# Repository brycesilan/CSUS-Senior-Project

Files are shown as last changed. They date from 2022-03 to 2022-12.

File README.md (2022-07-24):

# CSUS Senior Project
6AC1C5B5-E4C5-4D6C-B1AB-3A2F40A8B9AA

Vertical farming applies modern technologies to revolutionize the traditional agriculture process that has remained unchanged for millennia. Because traditional farming is limited in a 2D space it is very efficient at utilizing a given amount of land for food production. Transitioning the possible area, we can cultivate to a 3D space that can sustain exponentially larger yields than a traditional farm. Vertical farming uses a soilless method of growing food, meaning we can grow the food anywhere in the world with higher yields and fewer resources. With the human population on Earth exploding, the only way we can support the food demands of the future is to expand our food production capabilities into a whole new dimension… Up



A Collaboration with Silicon Valley Mechatronics
Banner2

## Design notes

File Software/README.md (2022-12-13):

# Software for semester 2

Our approach behind this project was to provide users with the hardware (everything connected)
- custom designed control board with loaded components
- Raspberry Pi 4 (With [Client-RaspberryPi](https://github.com/brycesilan/CSUS-Senior-Project/tree/main/Software/Client-RaspberryPi) code on it)
- Arduino Nano (with the [Moisture_pH.ino](https://github.com/brycesilan/CSUS-Senior-Project/blob/main/Software/Arduino/Moisture_pH/Moisture_pH.ino) script loaded on it)
- All the controls (4 pumps, 2 lights, 1 heater and 1 fan) hooked to the control board.
- All sensors (4 soil moisture and 1 pH sensors connected to the Arduino Nano, 1 DHT11 sensor connected to Raspberry Pi)

After setting up their farm, the user would sign up on our web app that was hosted on Firebase and receive a unique userID.

They would replace "User_ID" in [firebase-config.js](https://github.com/brycesilan/CSUS-Senior-Project/blob/main/Software/Client-RaspberryPi/firebase-config.js) and run "node index.js" from the terminal.
This would start sending sensor data to Cloud Firestore and update any controls (from user interface) every 15 seconds.

The user interface provides them with:
- Live sensor readings
- Buttons to control water pumps, lights, heater, and fan.
- Graph of daily readings (from 00:00 to 23:59 for the day)
- Ability to change farm settings (Either use buttons or automate the controls)

The overall goal was to provide the users with hardware and have them setup the farm. 
Then they could sign up on our web app (hosted on Firebase) and interact with their farm from anywhere.

## User Interface
User Interface was developed using Firebase, Cloud Firestore, React, Tailwind CSS, Chart.js.

The webapp developed using Firebase allows you to have multiple users

## Raspberry Pi
Raspberry Pi code developed using Node.js, Firebase, Cloud Firestore.

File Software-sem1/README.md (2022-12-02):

# Software for semester 1 (Archived)
Developed using Python, Flask, Arduino, HTML, Bootstrap

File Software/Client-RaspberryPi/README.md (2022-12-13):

# Client-Raspberry Pi code

The code in this folder runs on the Raspberry Pi.

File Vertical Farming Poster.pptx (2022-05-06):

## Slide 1

Vertical Farming
Elizabeth Tang, Ph.D. Department of Computer Science
College of Engineering and Computer Science

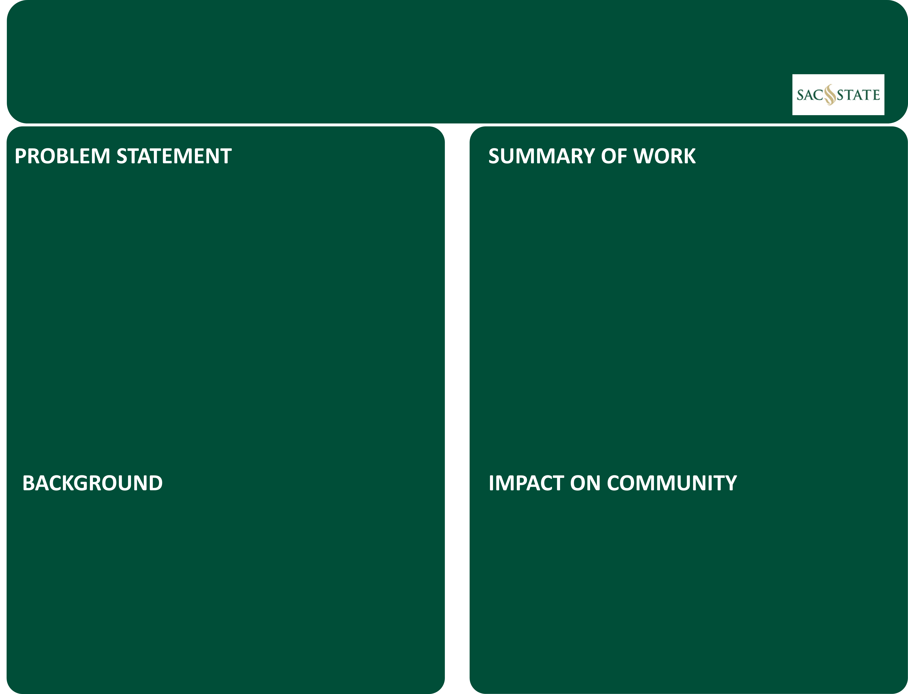
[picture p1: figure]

In this section, explain what you did , what you are doing, or what you plan to do. Keep things relatively simple. Drawings or pictures are often better than equations. Figures may be included here. Be sure to make reference to the Figure(s). In this section, explain what you did , what you are doing, or what you plan to do. Keep things relatively simple. Drawings or pictures are often better than equations. Figures may be included here. Be sure to make reference to the Figure(s).

In one, concise sentence, state what the problem is in laymen’s terms. Make reference to Figure 1 in that sentence.

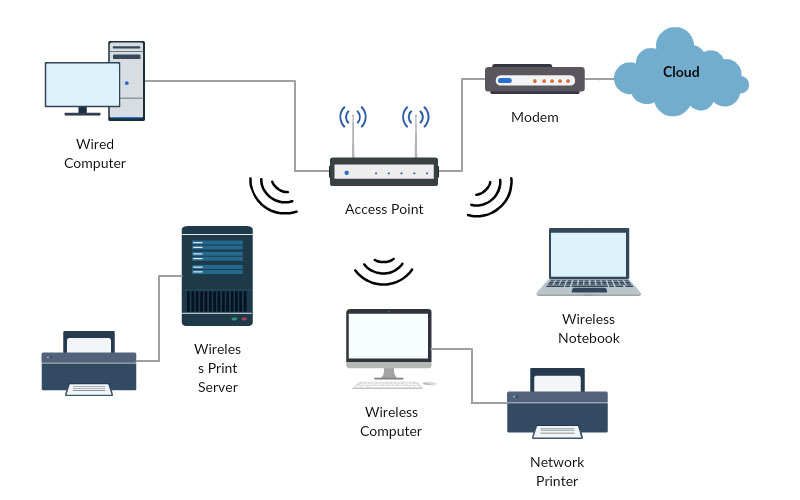
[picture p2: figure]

Figure 1: Add caption here. Add caption here. Add caption here. Add caption here. Add caption here. Add caption here..

In a short paragraph, provide background information necessary to help the guest understand the solution. Figures may be included here. Be sure to make reference to the Figure(s). In a short paragraph, provide background information necessary to help the guest understand the solution. Figures may be included here. Be sure to make reference to the Figure(s). In a short paragraph, provide background information necessary to help the guest understand the solution. Figures may be included here. Be sure to make reference to the Figure(s). In a short paragraph, provide background information necessary to help the guest understand the solution. Figures may be included here. Be sure to make reference to the Figure(s).

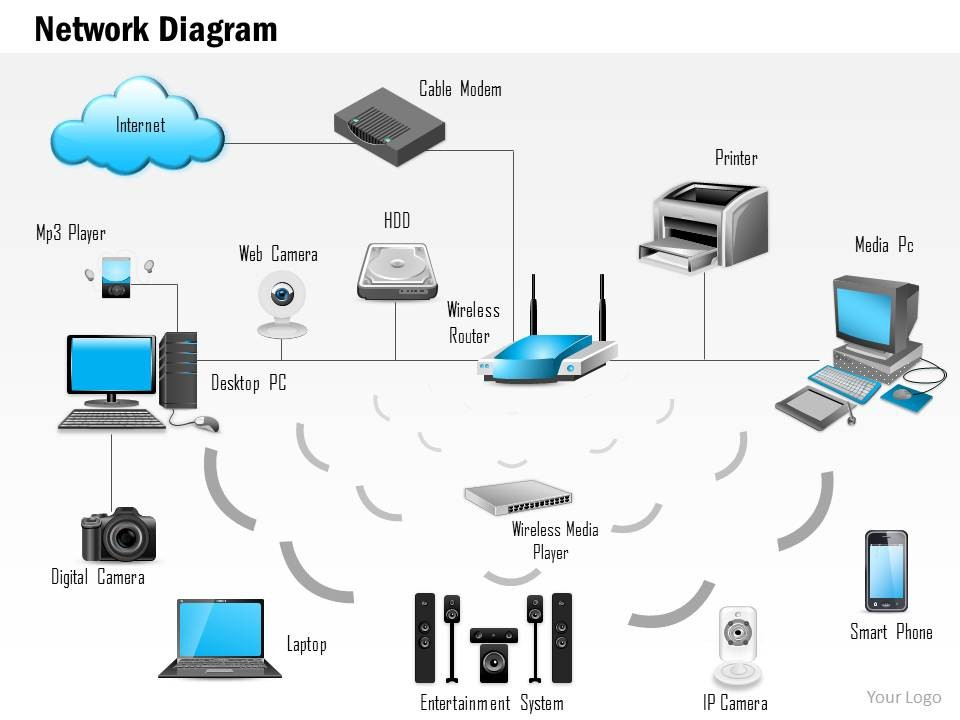
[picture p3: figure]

Figure 2: Add caption here. Add caption here.

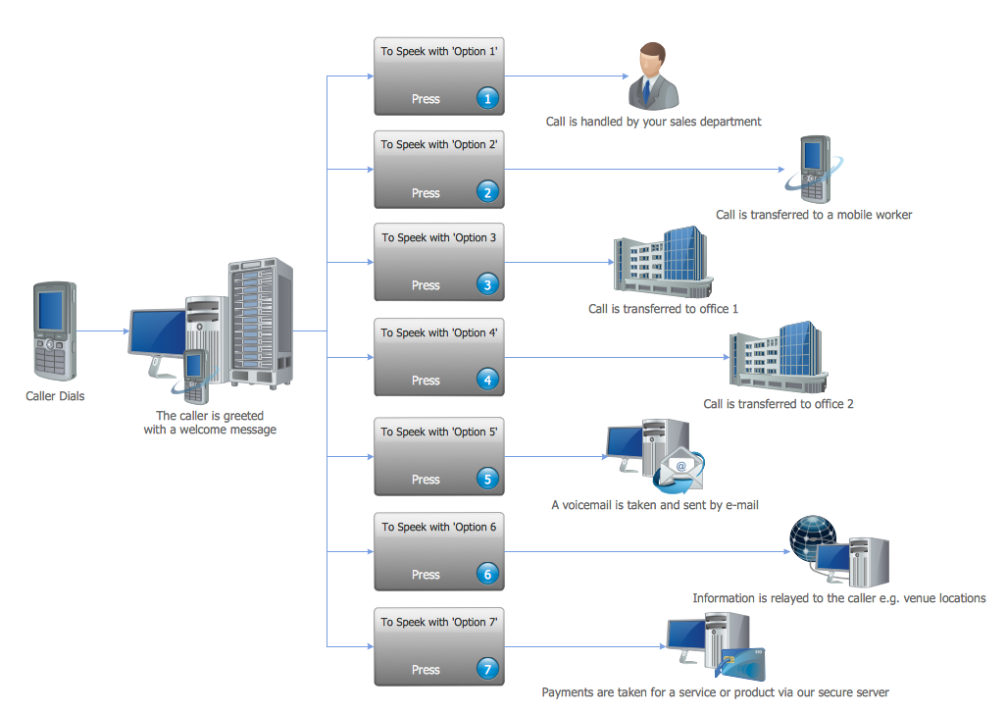
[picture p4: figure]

Figure 3: Add caption here. Add caption here.

What does this mean to the average American or to local industry? What does this mean to the average American or to local industry? What does this mean to the average American or to local industry? What does this mean to the average American or to local industry? What does this mean to the average American or to local industry? Bullet points are suggested:
- Bullet Point 1. Bullet Point 1. Bullet Point 1 . Bullet Point 1
- Bullet Point 2 . Bullet Point 2. Bullet Point 2. Bullet Point 2
- Bullet Point 3 . Bullet Point 2. Bullet Point 3. Bullet Point 3
- Bullet Point 4 . Bullet Point 4. Bullet Point 4..Bullet Point 4

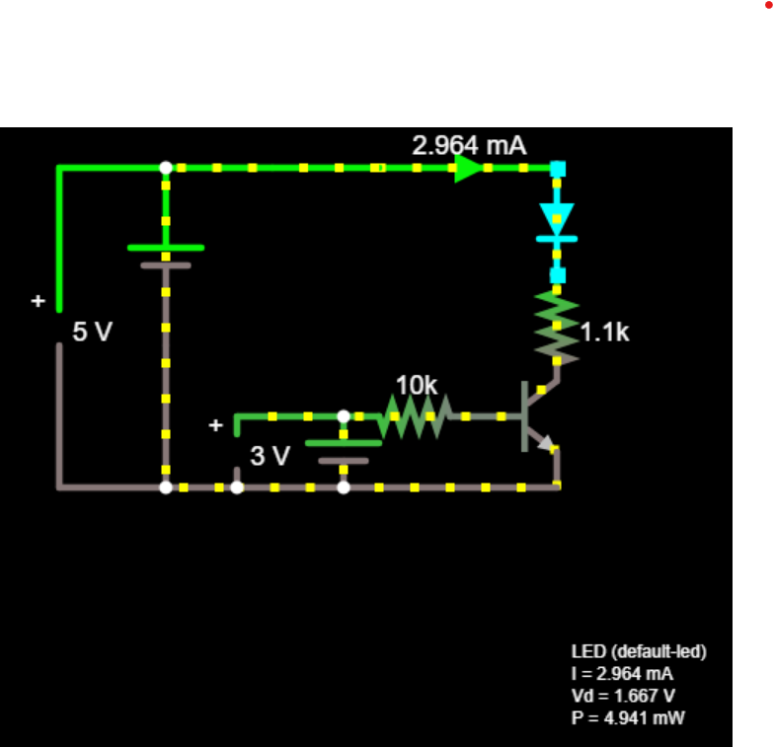
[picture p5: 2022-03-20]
Hardware/Moisture Sensor/Moisture Sensor Rev2/LED_Simulation.png

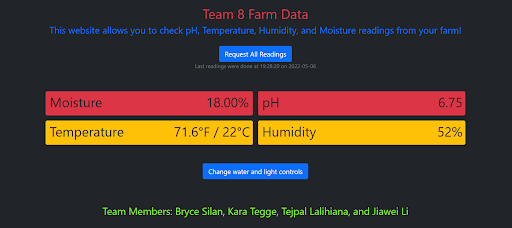
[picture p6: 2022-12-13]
Software-sem1/Screenshots/Readings page-sem 1.png

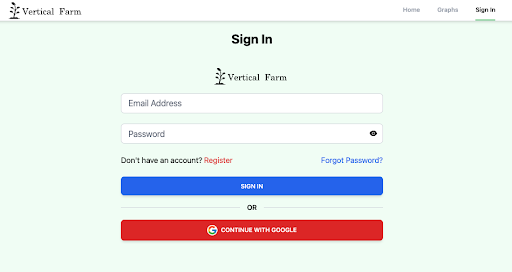
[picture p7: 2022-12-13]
Software/User-Interface/Screenshots/Sign-in page.png

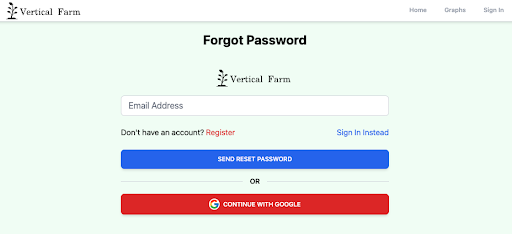
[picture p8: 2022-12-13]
Software/User-Interface/Screenshots/Forgot password page.png

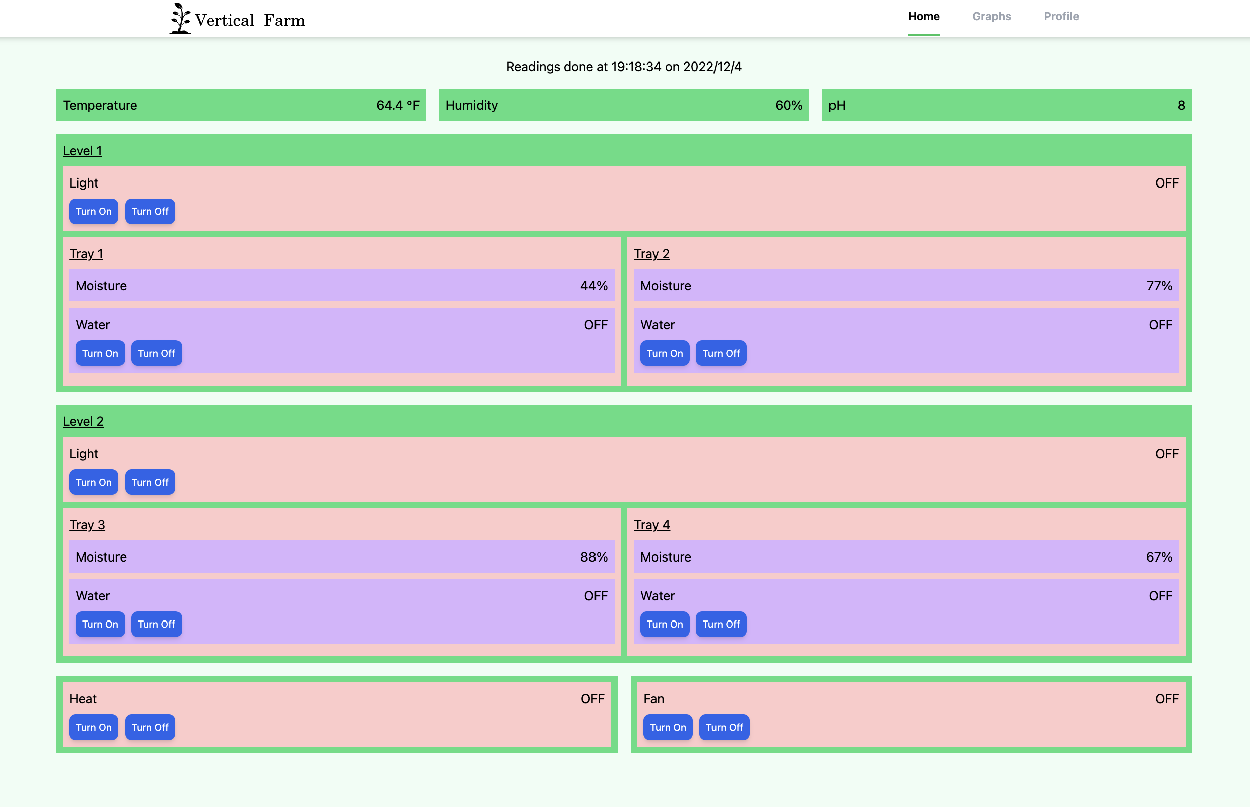
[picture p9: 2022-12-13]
Software/User-Interface/Screenshots/Home page.png

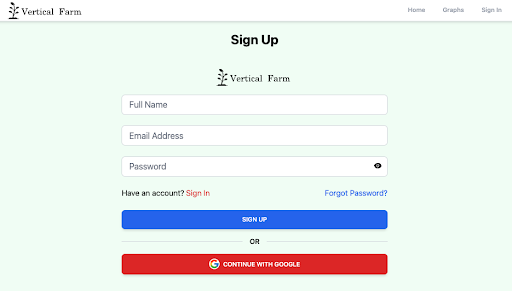
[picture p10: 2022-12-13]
Software/User-Interface/Screenshots/Sign-up page.png

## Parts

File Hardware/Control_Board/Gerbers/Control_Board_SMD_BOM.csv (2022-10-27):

Comment | Designator | Footprint
3.3uH | L1 | L_10.4x10.4_H4.8
10uF | C2,C1 | C_1206_3216Metric
6.8k | R6,R7 | R_0402_1005Metric
20k | R2 | R_0402_1005Metric_Pad0.72x0.64mm_HandSolder
LED_Red_power | D2,D1 | LED_0603_1608Metric
22uF | C5,C4 | C_1206_3216Metric
Q_Dual_PMOS_S1G1S2G2D2D2D1D1 | Q2 | SOP-8_3.9x4.9mm_P1.27mm
56.2k | R4 | R_0402_1005Metric
10k | R5,R3 | R_0402_1005Metric
TPS563200 | U3 | SOT-23-6
ULN2003 | U2,U1 | SOIC-16_3.9x9.9mm_P1.27mm
10k | R1 | R_0402_1005Metric_Pad0.72x0.64mm_HandSolder
PMOS | Q1 | SOIC-8_3.9x4.9mm_P1.27mm
100nF | C3 | C_0603_1608Metric

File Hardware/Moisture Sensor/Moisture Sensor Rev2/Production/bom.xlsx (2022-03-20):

Comment | Designator | Footprint | LCSC Part #（optional）
470pF | C1 | 402 | C1537 (https://lcsc.com/product-detail/Multilayer-Ceramic-Capacitors-MLCC-SMD-SMT_FH-Guangdong-Fenghua-Advanced-Tech-0402B471K500NT_C1537.html)
10uF | C2, C3 | 805 | C15850
100nF | C4, C7 | 402 | C1525 (https://lcsc.com/product-detail/Multilayer-Ceramic-Capacitors-MLCC-SMD-SMT_Samsung-Electro-Mechanics-CL05B104KO5NNNC_C1525.html)
10nF | C5 | 402 | C15195 (https://lcsc.com/product-detail/Multilayer-Ceramic-Capacitors-MLCC-SMD-SMT_Samsung-Electro-Mechanics-CL05B103KB5NNNC_C15195.html)
1uF | C6 | 603 | C15849 (https://lcsc.com/product-detail/Multilayer-Ceramic-Capacitors-MLCC-SMD-SMT_Samsung-Electro-Mechanics-CL10A105KB8NNNC_C15849.html)
1N4148 | D1 | SOD-323F | C2128 (https://lcsc.com/product-detail/Switching-Diode_Changjiang-Electronics-Tech-CJ-1N4148WS_C2128.html)
LED Red | D2 | 805 | C84256
LED Blue | D3 | 805 | C2293 (https://lcsc.com/product-detail/Light-Emitting-Diodes-LED_Hubei-KENTO-Elec-C2293_C2293.html)
50mA fuse | F1 | 1206 | C369153 (https://lcsc.com/product-detail/PTC-Resettable-Fuses_Jinrui-Electronic-Materials-Co-JK-NSMD005_C369153.html/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)
NPN BJT | Q1 | SOT-23-3 | C20526
330 | R1 | 402 | C25104 (https://lcsc.com/product-detail/Chip-Resistor-Surface-Mount_UNI-ROYAL-Uniroyal-Elec-0402WGF3300TCE_C25104.html)
1.5k | R2 | 402 | C25867
10k | R3, R7 | 402 | C25744 (https://lcsc.com/product-detail/Chip-Resistor-Surface-Mount_UNI-ROYAL-Uniroyal-Elec-0402WGF1002TCE_C25744.html)
1M | R4 | 402 | C26083 (https://lcsc.com/product-detail/Chip-Resistor-Surface-Mount_UNI-ROYAL-Uniroyal-Elec-0402WGF1004TCE_C26083.html)
1.1k | R5, R6 | 603 | C22764 (https://lcsc.com/product-detail/Chip-Resistor-Surface-Mount_UNI-ROYAL-Uniroyal-Elec-0603WAF1101T5E_C22764.html)
HT7550 | U1 | SOT-89-3 | C16106 (https://lcsc.com/product-detail/Dropout-Regulators-LDO_Holtek-Semicon-HT7550-1_C16106.html)
TLC555CDR | U2 | SOIC-8_3.9x4.9x1.27P | C6986 (https://lcsc.com/product-detail/Timer_Texas-Instruments-TLC555CDR_C6986.html)
OP07 | U3 | SOIC-8_3.9x4.9x1.27P | C7433 (https://lcsc.com/product-detail/Precision-OpAmps_Texas-Instruments-OP07CDR_C7433.html)

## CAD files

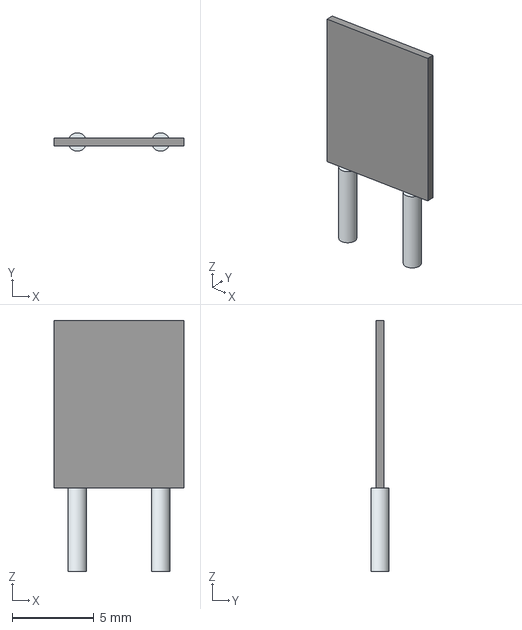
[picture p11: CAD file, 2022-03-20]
Electronics Local Library/1287-spade_tab_connector/3D/1287.stp
7.92 x 1.12 x 15.3 mm
Leads x 2

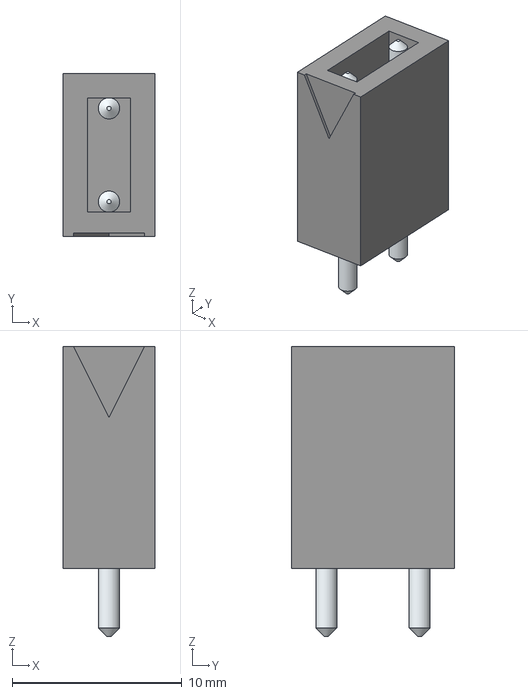
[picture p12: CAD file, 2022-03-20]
Electronics Local Library/39-28-8020/3D/39-28-8020.stp
5.40 x 9.60 x 17.1 mm
LeadsArray

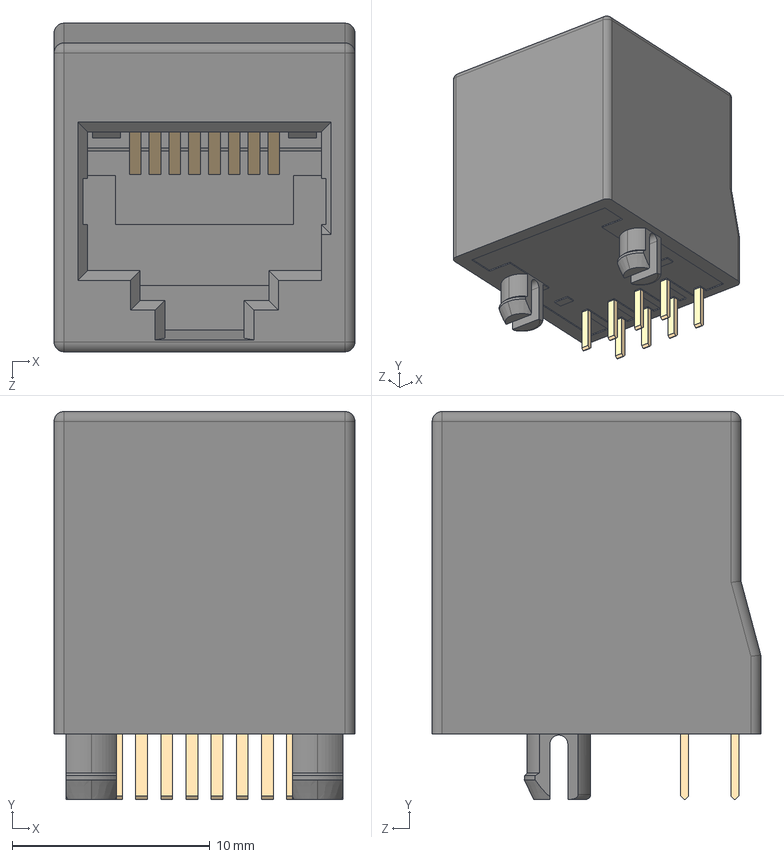
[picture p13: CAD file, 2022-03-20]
Electronics Local Library/3D Models/RJ45_VERT.STEP
15.2 x 19.6 x 16.6 mm

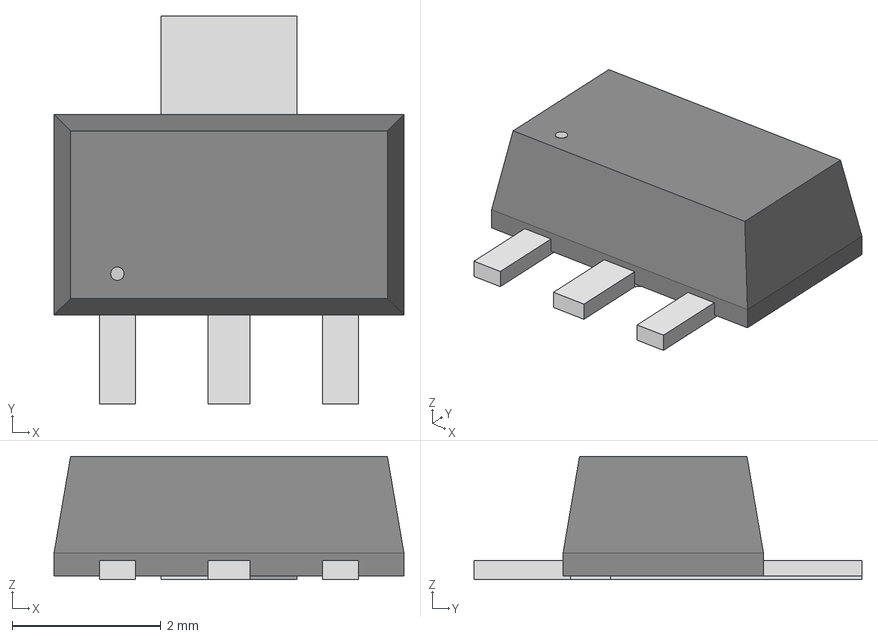
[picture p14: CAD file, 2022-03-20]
Electronics Local Library/HT75501SOT89TRLF/SOT89-3_HLT.step
4.70 x 5.21 x 1.65 mm

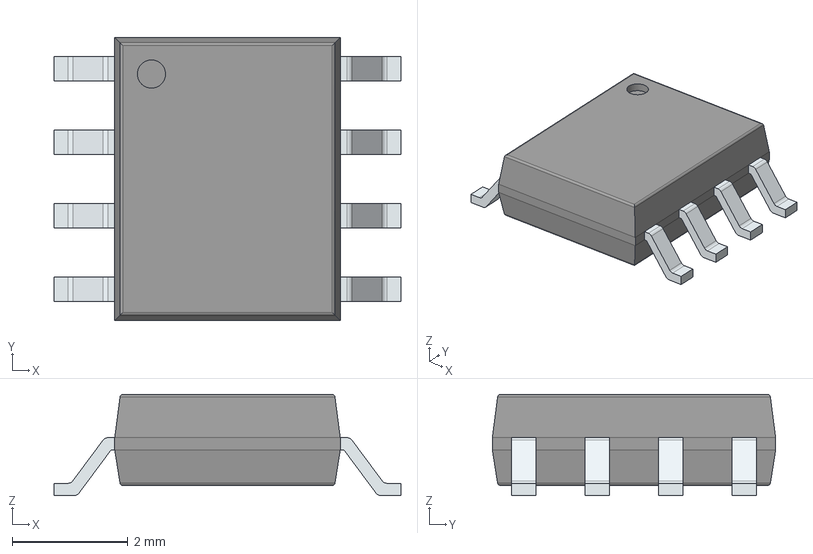
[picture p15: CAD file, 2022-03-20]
Electronics Local Library/P82B96TD,118/3D/P82B96TD,118.stp
6.00 x 4.90 x 1.75 mm
PinsArrayLR

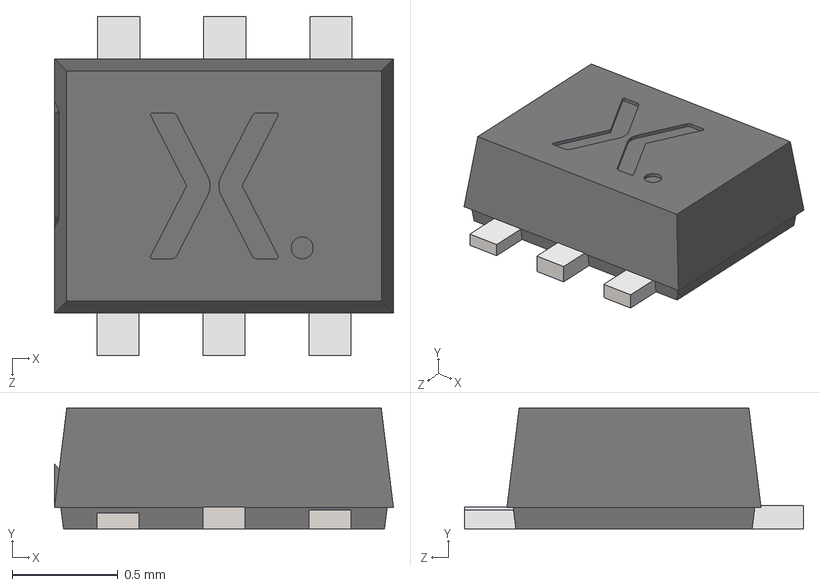
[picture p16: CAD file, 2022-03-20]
Electronics Local Library/PESD5V0L5UV,115/3D/PESD5V0L5UV,115.stp
1.60 x 0.57 x 1.60 mm
SOT666 Lower mold body
SOT666 LF
SOT666 upper mold body

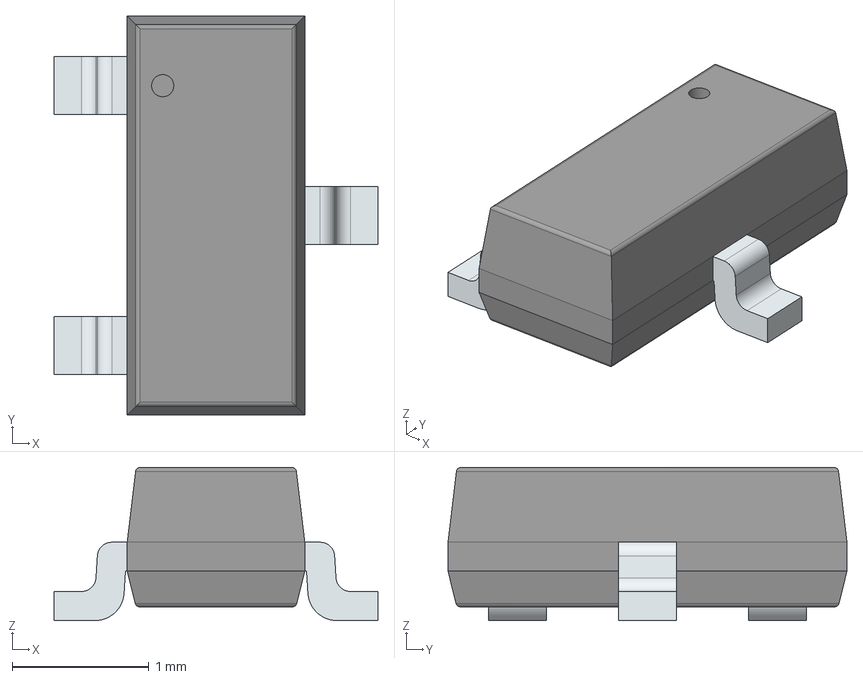
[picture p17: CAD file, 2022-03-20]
Electronics Local Library/SI2312CDS-T1-GE3/3D/SI2312CDS-T1-GE3.stp
2.37 x 2.92 x 1.12 mm
PinsArrayL
FilletPinR

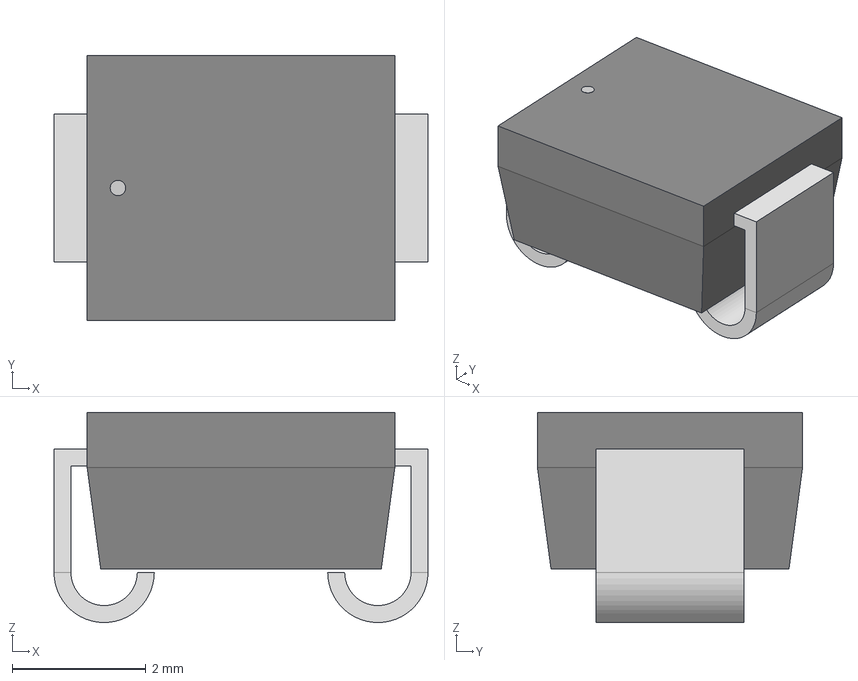
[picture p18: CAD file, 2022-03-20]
Electronics Local Library/SMBJ12ATR/SMBJ12ATR.step
5.59 x 3.96 x 3.14 mm

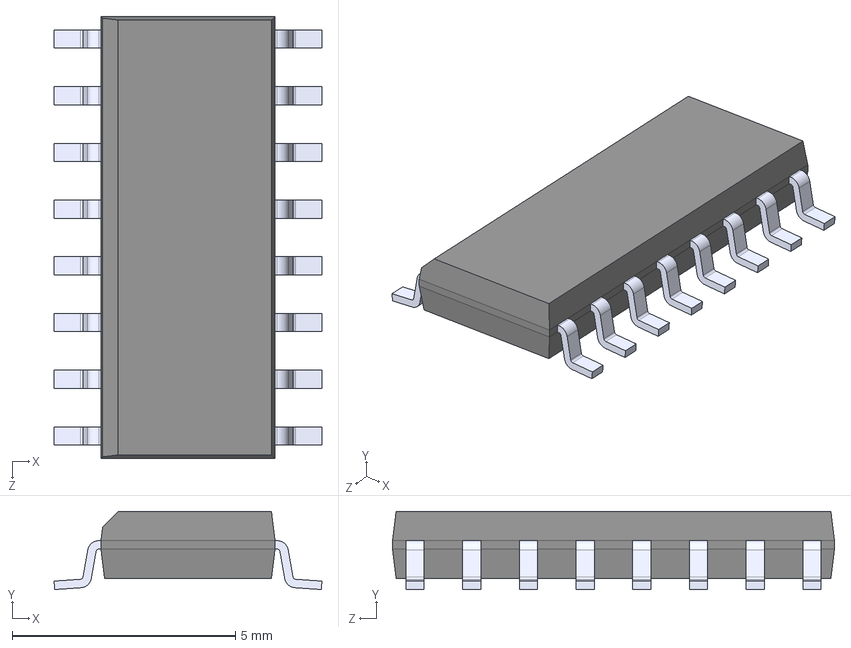
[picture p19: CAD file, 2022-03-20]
Electronics Local Library/SN74LV4051ADR/SN74LV4051ADR.step
6.00 x 1.75 x 9.90 mm

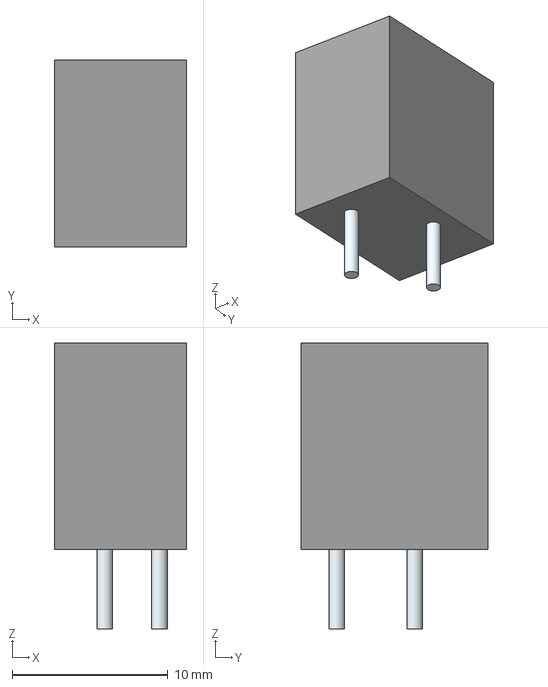
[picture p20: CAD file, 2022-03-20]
Electronics Local Library/TBL002A-350-02GY-2GY/3D/TBL002A-350-02GY-2GY.stp
8.50 x 12.0 x 18.4 mm
Leads x 2

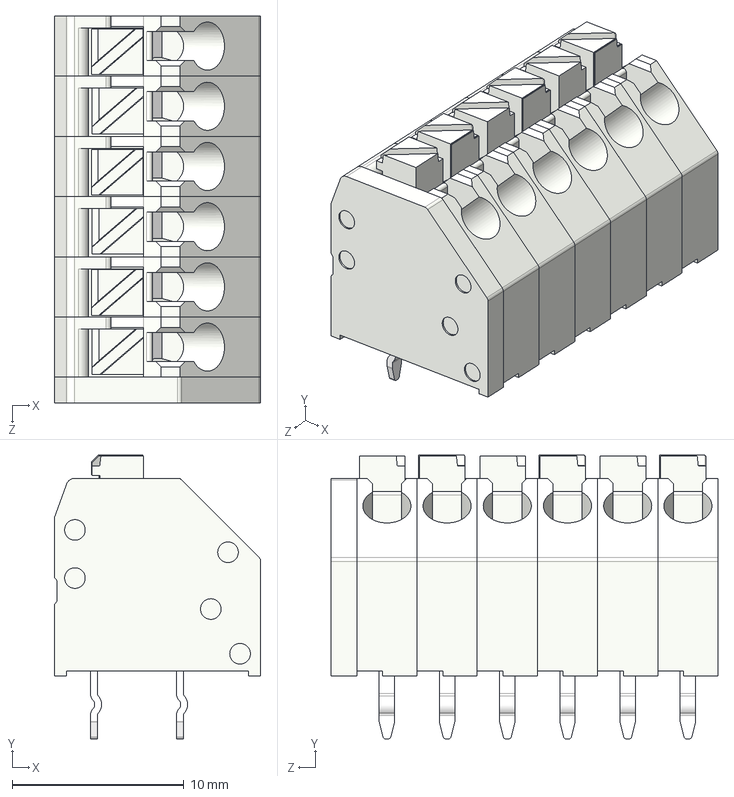
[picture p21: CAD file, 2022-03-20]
Electronics Local Library/TBL002A-350-06GY-2GY/CUI_DEVICES_TBL002A-350-06GY-2GY.step
12.0 x 16.5 x 22.5 mm
TBL002A-350 - END CAP_Gray
TBL002A-350 - BODY A_Gray x 3
TBL002A-350 - BODY B_Gray x 3
TBL002A-350 - PUSH BUTTON A_Gray x 3
TBL002A-350 - PUSH BUTTON B_Gray x 3

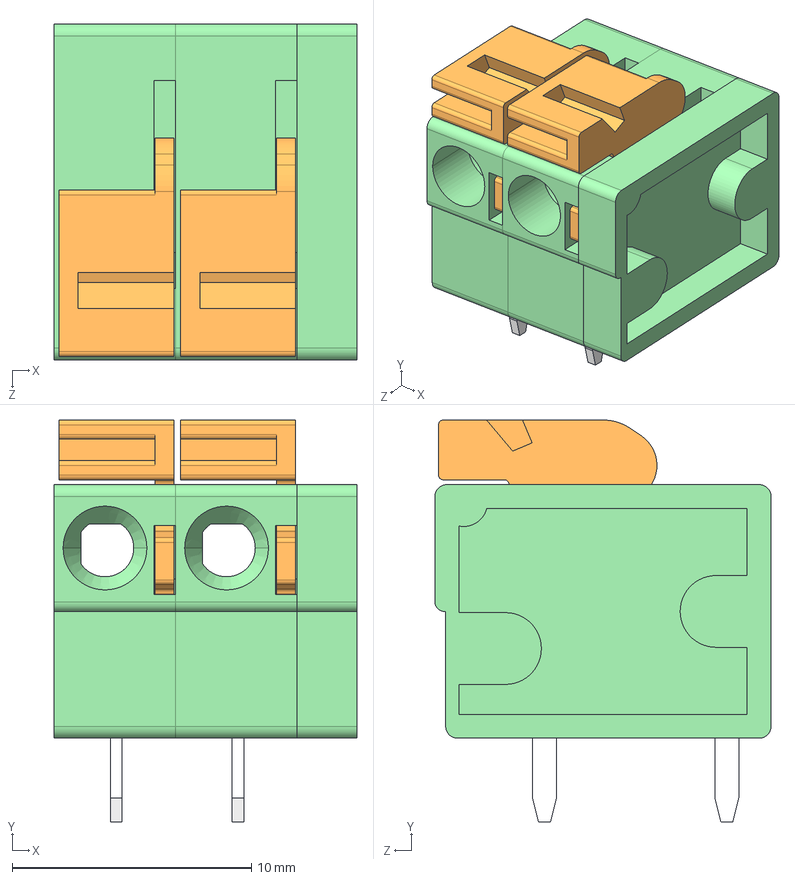
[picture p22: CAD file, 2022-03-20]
Electronics Local Library/TBL004-508-02BE-2GY/CUI_DEVICES_TBL004-508-02GR-2OR.step
12.7 x 16.8 x 14.1 mm
TBL004-508 - END CAP_Green
TBL004-508 - BODY_Green x 2
TBL004-508 - PUSH BUTTON_Orange x 2

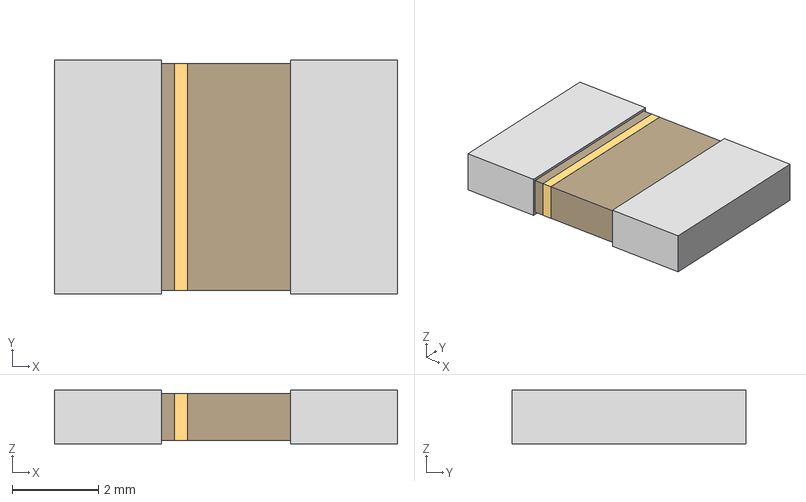
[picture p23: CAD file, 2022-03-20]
Electronics Local Library/3D Models/2920_SMD_FUSE.step
7.98 x 5.44 x 1.25 mm

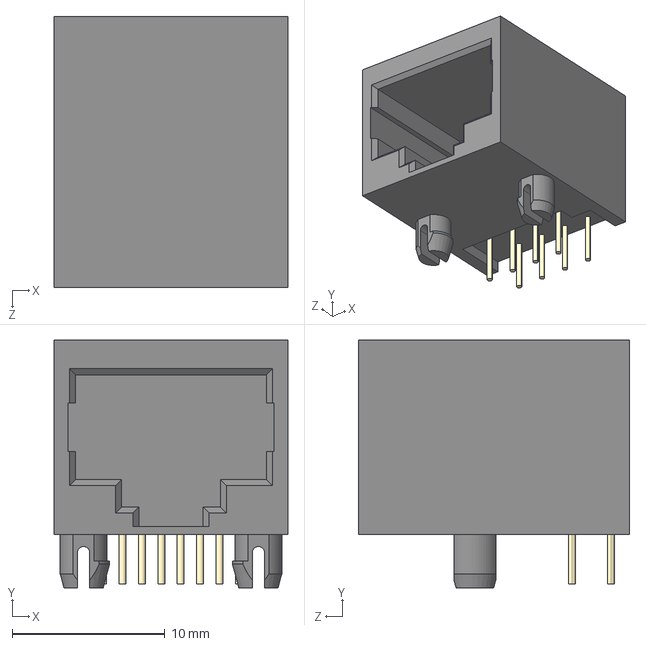
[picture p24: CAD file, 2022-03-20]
Electronics Local Library/54602-908LF/54602-908LF.step
15.3 x 16.2 x 17.7 mm

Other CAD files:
Electronics Local Library/1287-spade_tab_connector/3D/1287.stl
Electronics Local Library/39-28-8020/3D/39-28-8020.stl
Electronics Local Library/P82B96TD,118/3D/P82B96TD,118.stl
Electronics Local Library/SI2312CDS-T1-GE3/3D/SI2312CDS-T1-GE3.stl
Electronics Local Library/TBL002A-350-02GY-2GY/3D/TBL002A-350-02GY-2GY.stl

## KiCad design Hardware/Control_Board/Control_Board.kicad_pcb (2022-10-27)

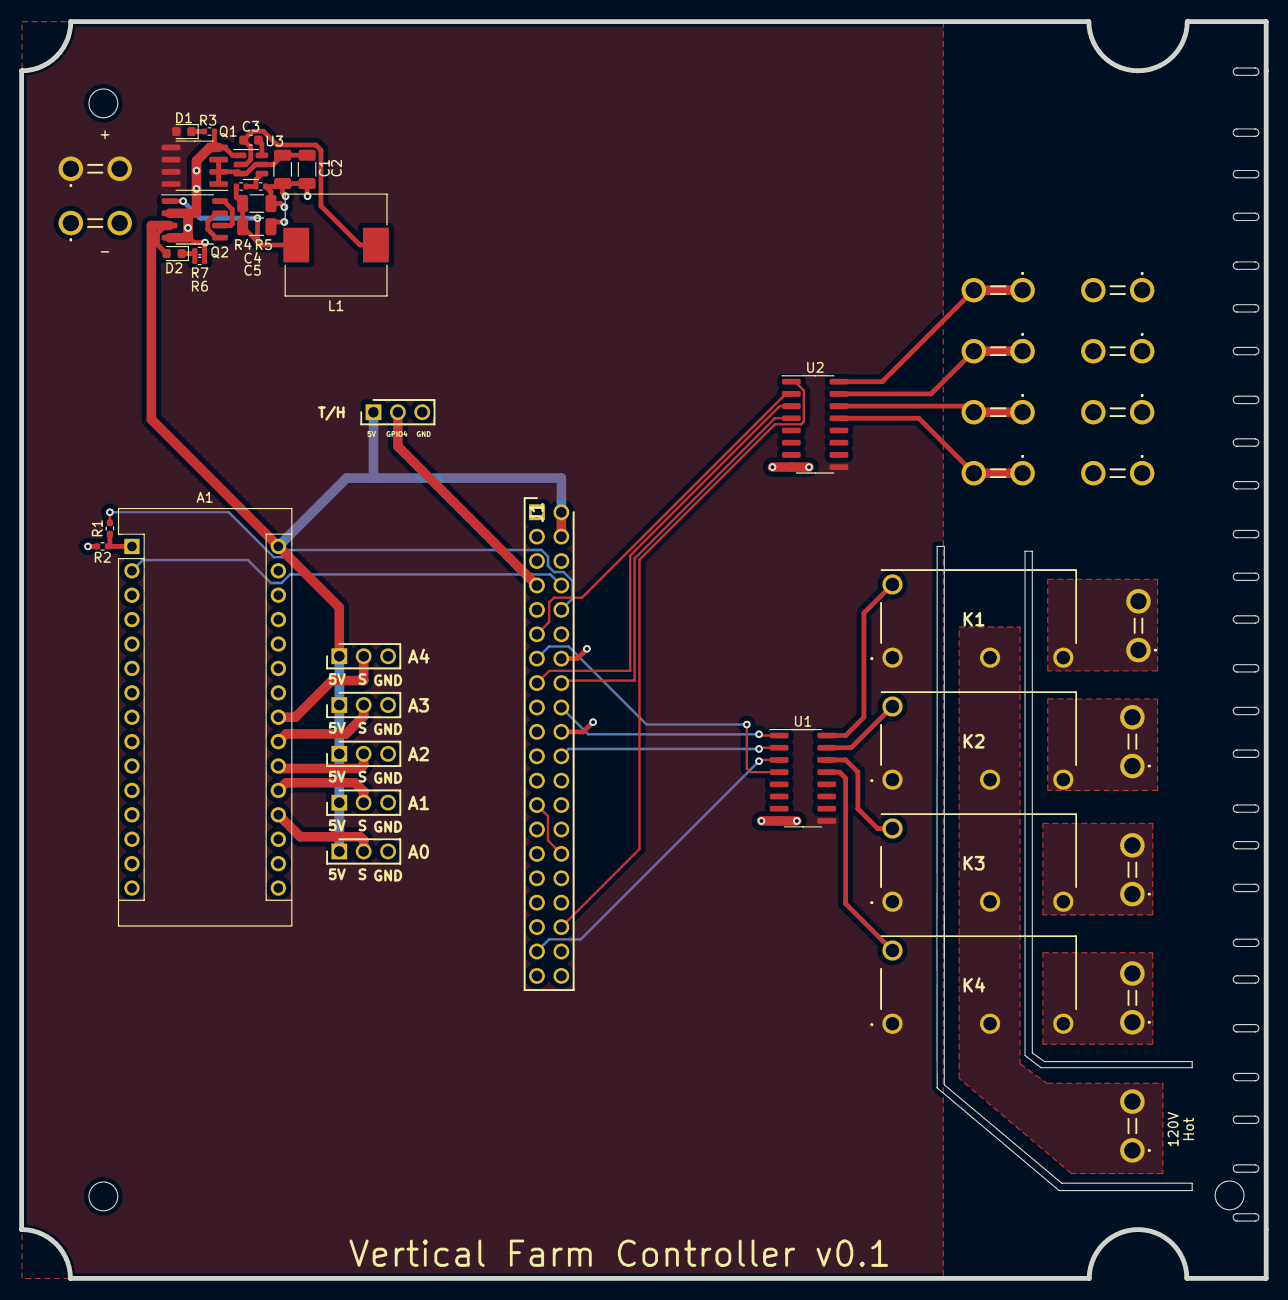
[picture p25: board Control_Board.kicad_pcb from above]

Board: 2 copper layers, 129.5 x 130.8 mm, 47 parts (0 on the bottom side), 41 nets.

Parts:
A0, A2, A3, A4: HDRV3W64P0X254_1X3_762X254X864P
A1: Arduino_Nano_v3.x; Arduino_Nano
A1#2: Arduino_Nano_v3.x; HDRV3W64P0X254_1X3_762X254X864P
C1, C2: 10uF; C_1206_3216Metric
C3: 100nF; C_0603_1608Metric
C4, C5: 22uF; C_1206_3216Metric
D1, D2: LED_Red_power; LED_0603_1608Metric
J1: Raspberry_Pi_2_3; HDRV40W64P254_2X20_5080X500X884P
J2, J3: Screw_Terminal_01x02; 197054301
J4, J5, J6, J8, J112: 19705-4301; 197054301
J**: 197054301
J**#2, J**#3, J**#4, J**#5, J**#6, J**#7, J**#8: 197054301
K1, K2, K3, K4: ALQ3F12; G5Q1A4DC24
L1: 3.3uH; L_10.4x10.4_H4.8
Q1: PMOS; SOIC-8_3.9x4.9mm_P1.27mm
Q2: Q_Dual_PMOS_S1G1S2G2D2D2D1D1; SOP-8_3.9x4.9mm_P1.27mm
R1: 10k; R_0402_1005Metric_Pad0.72x0.64mm_HandSolder
R2: 20k; R_0402_1005Metric_Pad0.72x0.64mm_HandSolder
R3, R5: 10k; R_0402_1005Metric
R4: 56.2k; R_0402_1005Metric
R6, R7: 6.8k; R_0402_1005Metric
T/H: HDRV3W64P0X254_1X3_762X254X864P
U1, U2: ULN2003; SOIC-16_3.9x9.9mm_P1.27mm
U3: TPS563200; SOT-23-6

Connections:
120V_Hot: J8.1, J8.2, K1.2 (NO), K2.2 (NO), K3.2 (NO), K4.2 (NO)
+5V: A0.1, A1.30 (VIN), A1#2.1 (D1/TX), A2.1, A3.1, A4.1, D2.2 (A), J1.2 (5V), J1.4 (5V), Q2.3 (S), T/H.1
+12V: D1.2 (A), J2.1, J2.2, K1.1 (Coil), K2.1 (Coil), K3.1 (Coil), K4.1 (Coil), Q1.5, Q1.6, Q1.7, Q1.8, U1.9 (COM), U2.9 (COM)
A0: A0.2, A1.19 (A0)
A1: A1.20 (A1), A1#2.2 (D0/RX)
A2: A1.21 (A2), A2.2
A3: A1.22 (A3), A3.2
A4: A1.23 (A4), A4.2
GND: A0.3, A1.4 (GND), A1.29 (GND), A1#2.3 (~RESET), A2.3, A3.3, A4.3, C1.2, C2.2, C4.2, C5.2, J1.6 (GND), J1.9 (GND), J1.14 (GND), J1.20 (GND), J1.25 (GND), J1.30 (GND), J1.34 (GND), J1.39 (GND), J3.1, J3.2, J**#2.1, J**#2.2, J**#4.1, J**#4.2, J**#5.1, J**#5.2, J**#7.1, J**#7.2, Q1.4, Q2.2 (G), Q2.4 (G), R2.2, R3.1, R5.1, R6.1, R7.1, T/H.3, U1.8 (GND), U2.8 (GND), U3.1 (GND)
unnamed: C1.1, C2.1, Q1.1 (D), Q1.2 (G), Q1.3 (eS), U3.3 (VIN), U3.5 (EN)
unnamed: C3.1, L1.1, U3.2 (SW)
unnamed: C3.2, U3.6 (VBST)
unnamed: C4.1, C5.1, L1.2, Q2.1 (S), R4.2
unnamed: D1.1 (K), R3.2
unnamed: D2.1 (K), R6.2, R7.2
unnamed: J1.10 (GPIO15/RXD), R1.1
unnamed: J4.1, J4.2, K1.3 (COM)
unnamed: J5.1, J5.2, K2.3 (COM)
unnamed: J6.1, J6.2, K3.3 (COM)
unnamed: J112.1, J112.2, K4.3 (COM)
unnamed: Q2.5 (D), Q2.7 (D)
unnamed: Q2.6 (G), Q2.8 (G)
unnamed: R4.1, R5.2, U3.4 (VFB)
Pump1: J**#3.1, J**#3.2, U2.16 (O1)
Pump2: J**#6.1, J**#6.2, U2.15 (O2)
Pump3: J**.1, J**.2, U2.14 (O3)
Pump4: J**#8.1, J**#8.2, U2.13 (O4)
RX: A1.1 (D1/TX), R1.2, R2.1
Relay1: K1.5 (Coil), U1.16 (O1)
Relay2: K2.5 (Coil), U1.15 (O2)
Relay3: K3.5 (Coil), U1.14 (O3)
Relay4: K4.5 (Coil), U1.13 (O4)
TX: A1.2 (D0/RX), J1.8 (GPIO14/TXD)
U1/Pin1: J1.18 (GPIO24), U1.1 (I1)
U1/Pin2: J1.22 (GPIO25), U1.2 (I2)
U1/Pin3: J1.37 (GPIO26), U1.3 (I3)
U1/Pin4: J1.13 (GPIO27), U1.4 (I4)
U2/Pin1: J1.36 (GPIO16), U2.1 (I1)
U2/Pin2: J1.11 (GPIO17), U2.2 (I2)
U2/Pin3: J1.15 (GPIO22), U2.3 (I3)
U2/Pin4: J1.16 (GPIO23), U2.4 (I4)

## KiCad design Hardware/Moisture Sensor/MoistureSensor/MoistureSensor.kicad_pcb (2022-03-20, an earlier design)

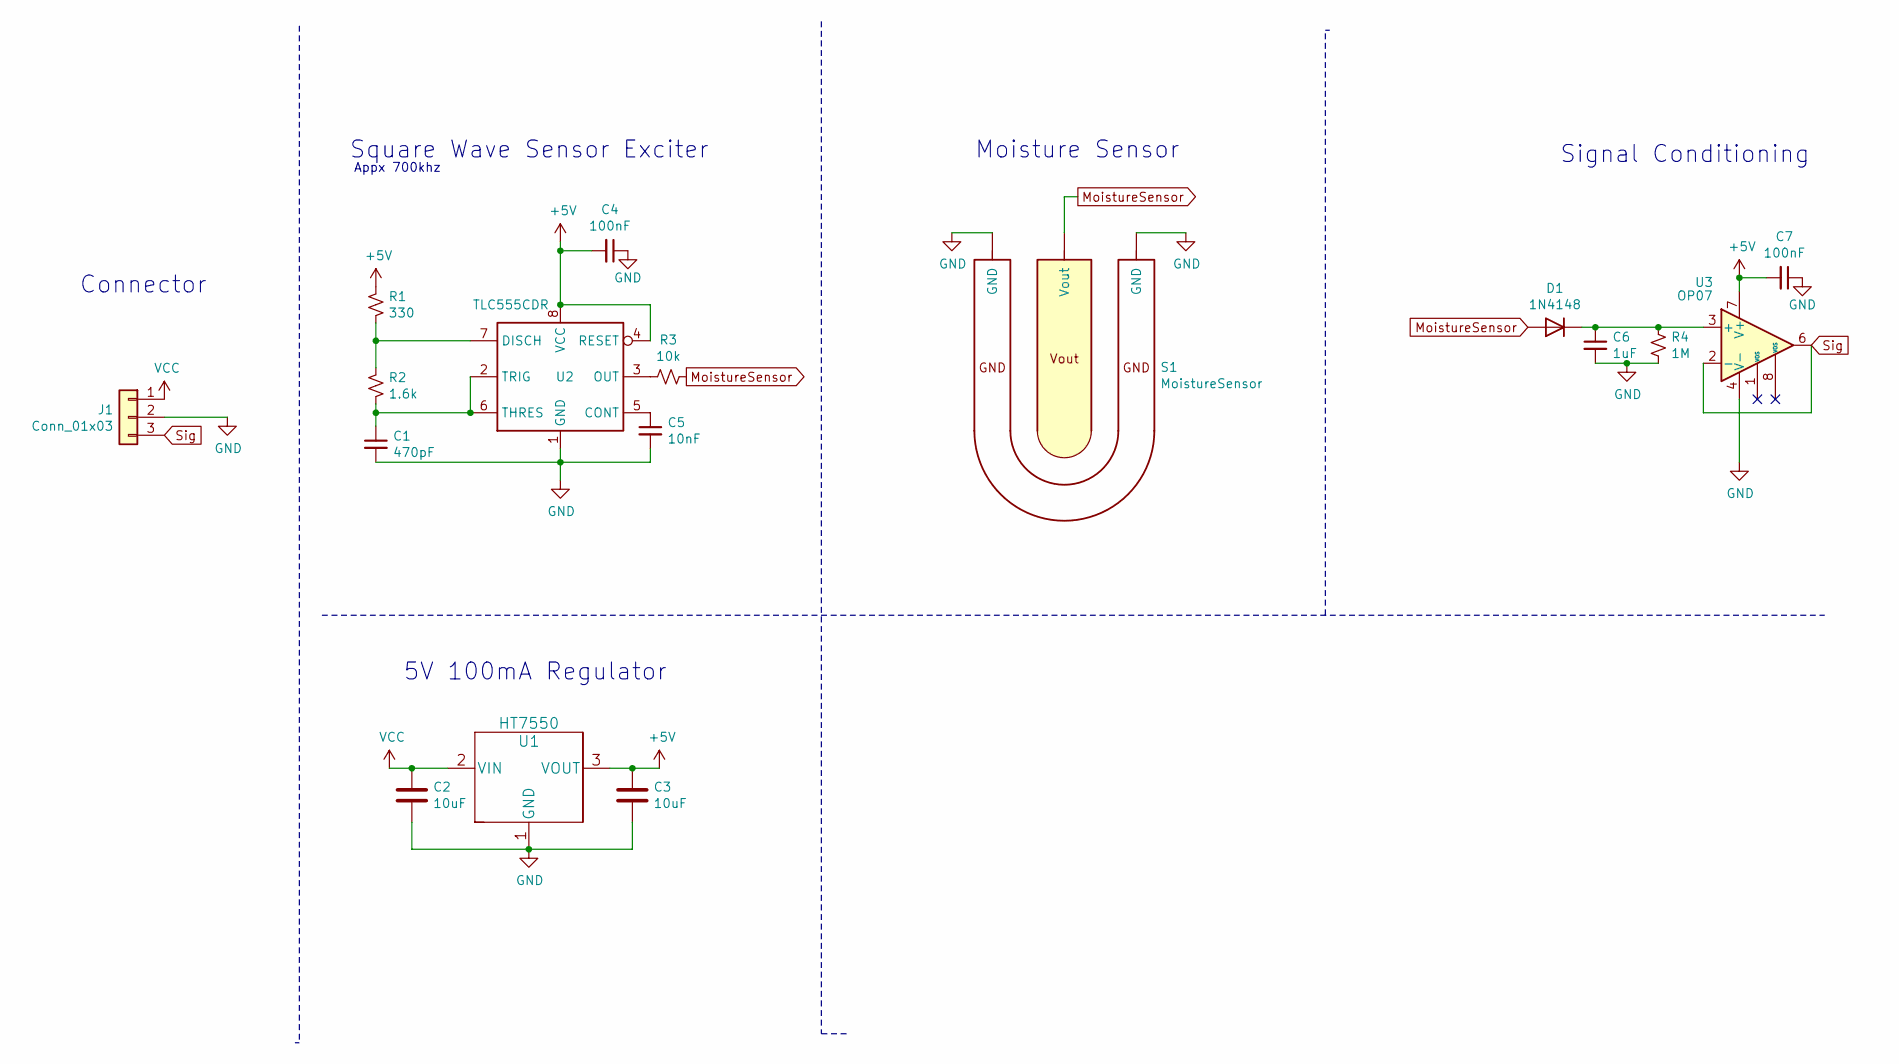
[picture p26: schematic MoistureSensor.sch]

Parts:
C1: 470pF; C_0402_1005Metric
C2, C3: 10uF; C_0805_2012Metric
C4, C7: 100nF; C_0402_1005Metric
C5: 10nF; C_0402_1005Metric
C6: 1uF; C_0603_1608Metric
D1: 1N4148; D_SOD-323F
J1: Conn_01x03; PinHeader_1x03_P2.54mm_Horizontal
R1: 330; R_0402_1005Metric
R2: 1.6k; R_0402_1005Metric
R3: 10k; R_0402_1005Metric
R4: 1M; R_0402_1005Metric
S1: MoistureSensor
U1: HT7550; HT7550-1-SOT89TRLF
U2: TLC555CDR; SOIC-8_3.9x4.9mm_P1.27mm
U3: OP07; SOIC-8_3.9x4.9mm_P1.27mm

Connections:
+5V: C3.1, C4.2, C7.2, R1.1, U1.3 (VOUT), U2.4 (RESET), U2.8 (VCC), U3.7 (V+)
GND: C1.2, C2.2, C3.2, C4.1, C5.2, C6.2, C7.1, J1.2, R4.2, S1.1 (GND), S1.3 (GND), U1.1 (GND), U2.1 (GND), U3.4 (V-)
MoistureSensor: D1.2 (A), R3.1, S1.2 (Vout)
unnamed: C1.1, R2.2, U2.2 (TRIG), U2.6 (THRES)
unnamed: C5.1, U2.5 (CONT)
unnamed: C6.1, D1.1 (K), R4.1, U3.3 (+)
unnamed: R1.2, R2.1, U2.7 (DISCH)
unnamed: R3.2, U2.3 (OUT)
Sig: J1.3, U3.2 (-), U3.6
VCC: C2.1, J1.1, U1.2 (VIN)

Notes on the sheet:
Appx 700khz
Square Wave Sensor Exciter
Moisture Sensor
Signal Conditioning
5V 100mA Regulator
Connector

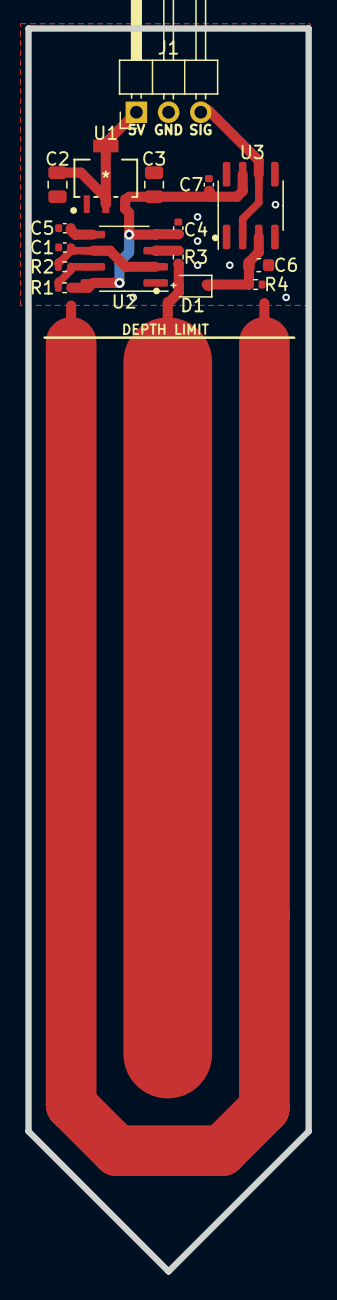
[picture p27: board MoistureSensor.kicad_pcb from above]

Board: 2 copper layers, 22.1 x 98.0 mm, 16 parts (0 on the bottom side), 10 nets.

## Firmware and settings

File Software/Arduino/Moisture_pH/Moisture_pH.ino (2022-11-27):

//Refer to Software-sem1/Moisture_and_pH/Moisture_and_pH.ino for previous moisture sensor code.
//Look at rh calculation and translate it to older/newer moisture sensors

float calibration_value = 23.85 - 0.4;

int pH_sensor_pin  = A0; //A0
int moisture_1_pin = A1; //A1
int moisture_2_pin = A2; //A2
int moisture_3_pin = A3; //A3
int moisture_4_pin = A4; //A4
int sampleSize = 6;
char incomingByte;

void setup() {
  Serial.begin(9600);
  Serial.println("1"); //Initial print to begin serial communication
}

void loop() {
  // put your main code here, to run repeatedly:

  //If you receive something at Serial, only then calculate and send sensor data back
  while (Serial.available() > 0)
  {
    incomingByte = Serial.read();
    //Serial.println(incomingByte);
    if (incomingByte == 'x')
    {
      outputValues();
    }

  }

}

void outputValues()
{
  float phValue = 0;
  int rh1 = 0, rh2 = 0, rh3 = 0, rh4 = 0;

  phValue = get_phValue();
  rh1 = get_rhValue(moisture_1_pin);
  rh2 = get_rhValue(moisture_2_pin);
  rh3 = get_rhValue(moisture_3_pin);
  rh4 = get_rhValue(moisture_4_pin);

  Serial.print("pH: ");
  Serial.println(phValue);
  Serial.print("Moisture_1: ");
  Serial.println(rh1);
  Serial.print("Moisture_2: ");
  Serial.println(rh2);
  Serial.print("Moisture_3: ");
  Serial.println(rh3);
  Serial.print("Moisture_4: ");
  Serial.println(rh4);
}

float get_phValue()
{
  float phValue = 0;
  float avgValue = 0;
  float voltage = 0;

  avgValue = calculateAverage(pH_sensor_pin);

  voltage = avgValue * (5.0 / 1024);
  phValue = -5.70 * voltage + calibration_value; //y=mx+b

  return phValue;
}

int get_rhValue(int moisturePin)
{
  float moistureAverage = 0;
  int rhValue = 0;

  //Calculate average moisture
  moistureAverage = calculateAverage(moisturePin);

  //Calculate relative humidity
  rhValue = calculateRH(moistureAverage);

  return rhValue;

}

float calculateAverage(int pinNumber)
{
  float sumOfReadings = 0; //Maybe change to unsigned long int if needed
  int analogReadings[sampleSize];

  //Take sampleSize number of readings 30ms apart
  for (int i = 0; i < sampleSize; i++)
  {
    analogReadings[i] = analogRead(pinNumber);

    delay(30);
  }

  for (int i = 0; i < sampleSize; i++)
  {
    sumOfReadings += analogReadings[i];
  }

  return sumOfReadings / sampleSize;
}

int calculateRH(float moistureAverage)
{
  float voltage = 0, rhFloat = 0;
  int rhValue = 0;

  voltage = moistureAverage * (5.0 / 1023.0); //Convert to voltage
  rhValue = -((63.2911 * voltage) - 171); //Convert to relative humidity

  rhValue = constrain(rhValue, 0, 100); //Make rhValue between 0 and 100

  return rhValue;
}

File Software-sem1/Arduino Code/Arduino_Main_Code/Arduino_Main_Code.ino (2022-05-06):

#define RELAY_1_PIN 2
#define RELAY_2_PIN 3 //WATER
#define RELAY_3_PIN 4
#define RELAY_4_PIN 5 //LIGHT

#define pH_SENSOR_PIN A0
#define MOISTURE_SENSOR_PIN A1

float calibration_value = 23.50 - 0.7; //This is for the pH Sensor

void setup()
{
  Serial.begin(9600);
  pinMode(RELAY_1_PIN, OUTPUT);
  pinMode(RELAY_2_PIN, OUTPUT);
  pinMode(RELAY_3_PIN, OUTPUT);
  pinMode(RELAY_4_PIN, OUTPUT);
}

void loop()
{
  if (Serial.available() > 0) {
    int relay = Serial.read() - '0';

    switch (relay) {
      case 1:
        Serial.println("RELAY 1");
        if (digitalRead(RELAY_1_PIN) == LOW) {
          digitalWrite(RELAY_1_PIN, HIGH);
          Serial.println("RELAY 1 ON");
        }
        else {
          digitalWrite(RELAY_1_PIN, LOW);
          Serial.println("RELAY 1 OFF");
        }
        break;
      case 2:
        Serial.println("RELAY 2");
        if (digitalRead(RELAY_2_PIN) == LOW) {
          digitalWrite(RELAY_2_PIN, HIGH);
          Serial.println("RELAY 2 ON");
        }
        else {
          digitalWrite(RELAY_2_PIN, LOW);
          Serial.println("RELAY 2 OFF");
        }
        break;
      case 3:
        Serial.println("RELAY 3");
        if (digitalRead(RELAY_3_PIN) == LOW) {
          digitalWrite(RELAY_3_PIN, HIGH);
          Serial.println("RELAY 3 ON");
        }
        else {
          digitalWrite(RELAY_3_PIN, LOW);
          Serial.println("RELAY 3 OFF");
        }
        break;
      case 4:
        Serial.println("RELAY 4");
        if (digitalRead(RELAY_4_PIN) == LOW) {
          digitalWrite(RELAY_4_PIN, HIGH);
          Serial.println("RELAY 4 ON");
        }
        else {
          digitalWrite(RELAY_4_PIN, LOW);
          Serial.println("RELAY 4OFF");
        }
        break;
      default:
        // wrong pin number, do nothing
        // all OUTOUTS will be powered off
        break;
    }
  }

  float ph = pH_code();
  float moisture = moisture_code();

  Serial.print("pH Value: ");
  Serial.println(ph);
  Serial.print("Moisture value: ");
  Serial.println(moisture);
}

float pH_code()
{
  float ph_val = 0;
  unsigned long int avg_val = 0;
  int sensor_readings[10];
  float volt = 0;

  for (int i = 0; i < 10; i++)
  {
    sensor_readings[i] = analogRead(pH_SENSOR_PIN);
    delay(30);
  }

  for (int i = 2; i < 8; i++)
  {
    avg_val += sensor_readings[i];
  }

  volt = (float)avg_val * 5.0 / 1024 / 6;
  ph_val = -5.70 * volt + calibration_value;

  return ph_val;
}

float moisture_code()
{
  float moisture_val = 0;
  unsigned long int avg_val = 0;
  int sensor_readings[10];
  float voltage;
  float rh;
  int rh_val;

  for (int i = 0; i < 10; i++)
  {
    sensor_readings[i] = analogRead(MOISTURE_SENSOR_PIN);
    delay(30);
  }

  for (int i = 2; i < 8; i++)
  {
    avg_val += sensor_readings[i];
  }

  voltage = avg_val * (5.0 / 1023.0) / 6;
  rh = (((voltage - 4.4) * -1) * 90);

  rh = constrain(rh, 0, 100);

  rh_val = rh;
  rh_val = constrain(rh_val, 0, 100);

  return rh_val;
}

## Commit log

2022-03-20 First iteration of hardware designs
    [1287.stl, 1287.stp, 2920_SMD_FUSE.step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]
2022-04-13 Update with single button requesting multiple sensor readings
2022-04-22 Add Moisture and pH sensor Arduino Code
2022-04-22 Correct pH sensor Arduino code
    [pH.ino]
2022-04-22 Hardware updates
    [BOM.xlsx, BOM_noTH.xlsx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]
2022-04-26 separate temperature,ph functions and add water control to index.html
2022-04-26 Code cleanup and add timer to check main function runtime
2022-04-27 Modify app.py to read moisture and ph from the same Arduino
2022-05-06 Add data logging capability to app.py
    [Sensor-Data.csv]
2022-05-06 Added relay control
2022-05-06 Add auto-refresh functionality
    [Sensor-Data.csv]
2022-05-06 Add pin configurations
    [Sensor-Data.csv]
2022-05-06 Incomplete working code with light control
    [Sensor-Data.csv]
2022-05-07 Light and water working
    [Sensor-Data.csv]
2022-05-07 Code cleanup and working
    [Sensor-Data.csv]
2022-05-11 Change to 'Get sensor readings'
    [Sensor-Data.csv]
2022-05-11 Correct pH calibration values
    [Moisture_and_pH.ino]
2022-08-02 Added Control_Board
    [Control_Board.kicad_pcb, Control_Board.kicad_sch]
2022-09-18 Control board updates
    [Control_Board.kicad_sch]
2022-09-18 Sch rev 1 ready for review
    [Control_Board.kicad_sch]
2022-09-18 Cleaned up hardware repo
    [Adapter (2).kicad_pcb, Adapter BOM.csv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]
2022-09-19 Control board layout
    [Control_Board.kicad_pcb, Control_Board.kicad_sch]
2022-10-06 Move semester 1 software to Software-sem1 folder
    [Sensor-Data.csv]
2022-10-09 PCB layout additions
    [Control_Board.kicad_pcb]
2022-10-09 PCB layout updates
2022-10-13 Control_Board updates
    [Control_Board.kicad_pcb, Control_Board.kicad_sch]
2022-10-19 Board updates, ready for power regulation component placements
    [Control_Board.kicad_pcb]
2022-10-20 Laid out power regulation stuffs
    [Control_Board.kicad_pcb]
2022-10-25 Updated Analog sensor routing
    [Control_Board.kicad_pcb]
2022-10-25 v0.1 Ready for review
    [Control_Board.kicad_pcb]
2022-10-25 Vertical fix
    [Control_Board.kicad_pcb]
2022-10-25 Schematic hotfix
    [Control_Board.kicad_pcb, Control_Board.kicad_sch]
2022-10-26 v0.1 Gerbers
    [Control_Board-B_Cu.gbr, Control_Board-B_Mask.gbr, Control_Board-B_Paste.gbr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]
2022-10-30 Update Arduino code to use 4 moisture sensors (not tested)
2022-11-02 Move Moisture_pH.ino to Arduino/
    [Sensor-Data.csv]
2022-11-14 Remove unnecessary serial prints
2022-11-15 Sensor read working
2022-11-16 create Reading object after reading from sensors
2022-11-20 Add date, correct serial read
    [index.js, test.js]
2022-11-21 Add flowing LED test script to test RPi GPIO
2022-11-26 Push values to firestore Current and daily document working
2022-12-05 Automation and buttons working

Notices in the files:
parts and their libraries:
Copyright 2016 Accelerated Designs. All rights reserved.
